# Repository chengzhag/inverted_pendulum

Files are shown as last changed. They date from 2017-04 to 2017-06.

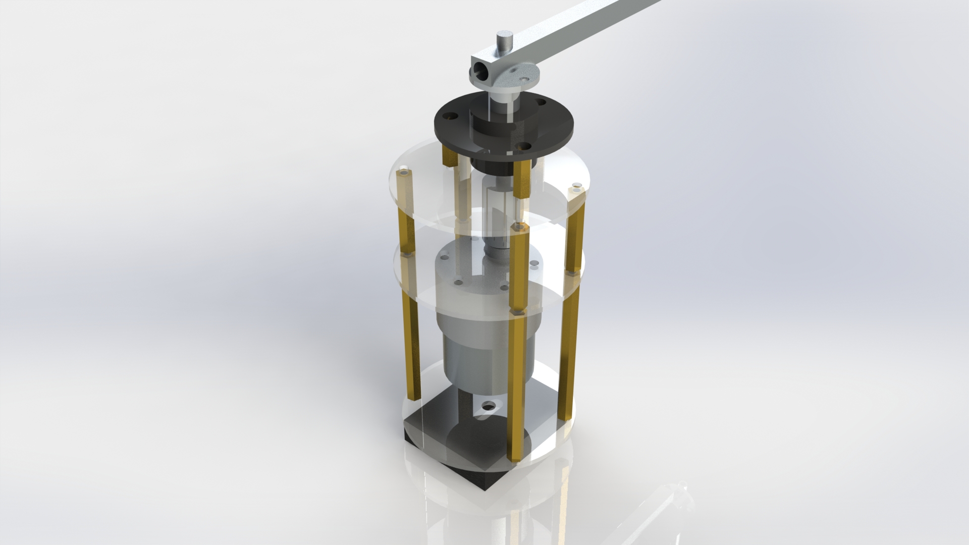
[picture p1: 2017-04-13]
3d/装配体/驱动部分渲染图.JPG

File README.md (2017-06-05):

# inverted_pendulum

电子科技大学2017电子设计竞赛校队控制组第一次训练，KZ-3组

小组成员：章程，韦仕才，徐瑶

采用ebox库，vs2015开发环境。[模板和使用说明](https://github.com/pidan1231239/ebox_stm32f103RCT6_VS#ebox_stm32f103rct6_vs)参考队长[章程](https://github.com/pidan1231239)的ebox_stm32f103RCT6_VS

## 机械部分说明

### 材料选取及用途：
- 3mm厚碳板和铜柱作为快装板和电机支撑
- 碳方管作为横梁
- 碳圆管作为摆杆
- 铝棒作为转轴
- 底部用三脚架支撑
- 连接处用法兰联轴器以及五转六的电机联轴以及绑扎带固定
- 采用导电滑环防止绕线

## 软件部分说明

### 重新编写编码器驱动```encoder_timer```
- 可用引脚：高级定时器和通用定时器可以将ch1和ch2配置成正交编码器AB相输入
- TIM1~TIM4可用io口如下：
  - TIM1:PA8 PA9
  - TIM2:PA0 PA1
  - TIM3:PA6 PA7
  - TIM4:PB6 PB7
- 本次倒立摆设计采用TIM1和TIM3配置正交编码器。用TIM2配置PWM控制电机

### 编写电机驱动```encoder_motor.h```
- 设置速度和位置模式以及PID初始化

### 将光编码器作为绝对编码器使用
- 计算摆杆的角加速度和角速度，以弧度制为单位

### 采用四级PID控制
- 对摆杆角度、摆杆角速度、横梁角度、横梁角速度进行PID算法控制

### 采用状态机和四个独立键盘对倒立摆进行模式切换
- 选择io如下：PB12 PB13 PB14 PB15
- 对应模式：```Swing SwingInvert Invert Round```

### 用freertos设置进程
- 实现多任务并行处理

## 电路部分说明
- 电路组成：
  - LM2596S-5.0作为降压模块
  - tb6612作为电机驱动
  - stm32f103c8t6最小系统作为主控
  - 四个独立按键
- 电路设计：
  - 电机驱动模块插座
  - c8t6最小系统板插座
  - 降压模块插座
  - 4pin xh2.56光编码器接口
  - 6pin xh2.56电机接口
  - 4pin xh2.56延长线
  - 12v电池插头

## 有限状态机
### 设计思路
- 状态以类的方式存储
- 状态的entry、work、exit函数以指针方式存储
- 状态的向外转移列表以类链表存储

### class FiniteStateMachine
> 有限状态机类
- 切换状态
  - 执行上一个State的exit函数
  - （执行状态转移函数，需要状态过渡时使用）
  - 设置当前状态指针
  - 执行下一个State的entry函数
- refresh函数中
  - 调用状态的work函数
  - 判断是否满足下列条件，如果满足，进行转移
    - 满足状态的向外转移列表中事件对应的bool判别式（函数，传入event参数）

### class FiniteStateMachineState
> 状态类
- 包含entry、work、exit函数指针
  - 提供接口对函数指针进行初始化
  - 提供接口对函数指针进行调用
- 向外转移列表（链表）
  - 在FiniteStateMachine调用refresh进行转移判断时对当前State的列表进行遍历，满足条件则进行转移
  - 提供接口addTransItem用以增加表项
  - 在初始化时可直接将该表传入

### class FiniteStateMachineTrans
> 向外转移列表类，单向链表，自身构成链表头
- 通过next指针形成链表
- 在初始化时可通过before衔接已有的链表
- 包含一个bool代数式（函数）condition
- 包含一个目标State*（状态指针）

### 改进方向
- FiniteStateMachineState添加向外转移表项的函数改为可变参数
- 改进FiniteStateMachineTrans类为FiniteStateMachineTransList和FiniteStateMachineTransItem，成为一个封装完善的单向链表，且具有添加操作
- 考虑以unsigned long型保存event，用多选一的方式表示单个event，这样可以通过或操作完成多个event的表示，将event和condition分离，以event作为触发，condition作为条件

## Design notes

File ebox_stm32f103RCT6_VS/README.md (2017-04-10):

# 第41组软件方向说明

## 1 工程模板

> stm32 + ebox的工程模板已发布到[github](https://github.com/pidan1231239/ebox_stm32f103RCT6_VS)上
在压缩包中对应文件：**ebox_stm32f103RCT6_VS.zip**

- 开发环境采用Visual Studio 2015 + visualGDB，编译器采用keil5的arm编译器，配置过程参考文件：**Visual Studio搭建STM32开发环境（自动补全+跳转+DEBUG**
- 了解ebox的功能和已包含驱动，访问[ebox官网](http://www.eboxmaker.com/)和参考上方github链接中[包含驱动](https://github.com/pidan1231239/ebox_stm32f103RCT6_VS/blob/master/README.md#包含驱动)
- 深入了解[stm32 ebox工程从keil到visual studio的迁移过程](https://github.com/pidan1231239/ebox_stm32f103RCT6_VS/blob/master/README.md#如何将工程搬移到visualgdb上)，和[visualGDB官方教程](https://visualgdb.com/tutorials/arm/keil/)

## 2 开发环境

> 以下必备开发软件务必都装在默认位置！尤其是keil 5，因为visualGDB的工程使用了keil的编译器，引用的是绝对地址

### 2.1 Visual Studio 2015 Community

> 在Microsoft官网下载免费版，并更新至update3

### 2.2 keil 5

> 安装keil for arm，即mdk

### 2.3 VisualGDB

> 安装visualgdb 5.16，文件：**visualgdb516rpj(www.greenxf.com).zip**

### 2.4 VassistX

> 安装VisualAssistX 10.9.2108，文件：**[WWW.WuleBa.COM]Vis.ual.Ass.ist.X 10.9.2108 官.方.原.版+破@jie补丁（Visual Studio 超强插件，吾乐吧软件站分享）.rar**

> 以上环境的配置参考文件:**Visual Studio搭建STM32开发环境（自动补全+跳转+DEBUG）.pdf**

### 2.5 Visual Studio Code

编辑MarkDown，浏览代码等

### 2.6 gihub gui客户端

版本控制，代码共享、合作

## 3. 开发硬件

### 3.1 STM32 F103

> 受限于ebox库，目前任得到维护的只有针对STM32 F103的ebox

### 3.2 RL78/G13 开发套件 R5F100LEA 单片机

> 一款瑞萨的单片机开发板，校队可能会发，为前几届比赛个别控制体的指定用MCU

### 3.3 可能需要的基于linux的开发板，如树莓派

> 图像处理等大计算量运算

## 4 必备技能

### 4.1 C++

> - 要求掌握对象、继承、重载、模板、命名空间等常用知识
> - 开发单片机用

### 4.2 MarkDown

> - 学习此文档中使用的一些基本语法
> - 用于代码文档的编写

### 4.3 github gui客户端

> - 注册github账号，完成官方基础教程
> - 下载安装GitKraken和SourceTree

### 4.4 matlab

> - 用于算法的实验、学习控制理论
> - 其他未知用途

### 4.5 印象笔记

> - 下载手机、电脑客户端
> - 注册账号
> - 记录重要事件
> - 记录分享赛题资料、思考，协同编辑

### 4.6 Processon

> - 一款在线作图应用
> - 注册账号
> - 实时协作
> - 常用系统框图和流程图、思维导图等

### 4.7 SolidWorks 2017

> - 三维制图，零件、装配体
> - 工程图生成：装配图、零件图、剖面、三视图

## 5 统一编程命名规范

- 类名采用首字母大写的驼峰命名法：```class EncoderMotor```
- 函数、变量采用首字母小写的驼峰命名法：```int motorPosition```
- 宏定义，全大写，单词之间用"_"隔开：```#define ENCODER_MOTOR```
- 枚举变量，enum用首字母大写的单词，以"_"隔开：
```cpp
typedef enum
{
  EXTI_Trigger_Rising = 0x08,
  EXTI_Trigger_Falling = 0x0C,  
  EXTI_Trigger_Rising_Falling = 0x10
}EXTITrigger_TypeDef;
```

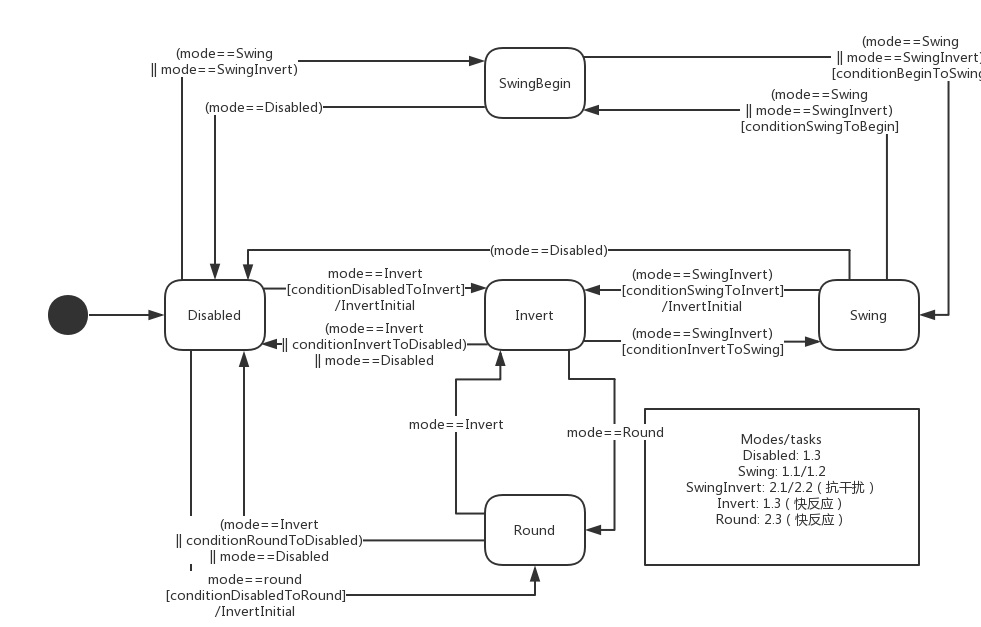
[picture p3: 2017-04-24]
文档/倒立摆状态机.jpg

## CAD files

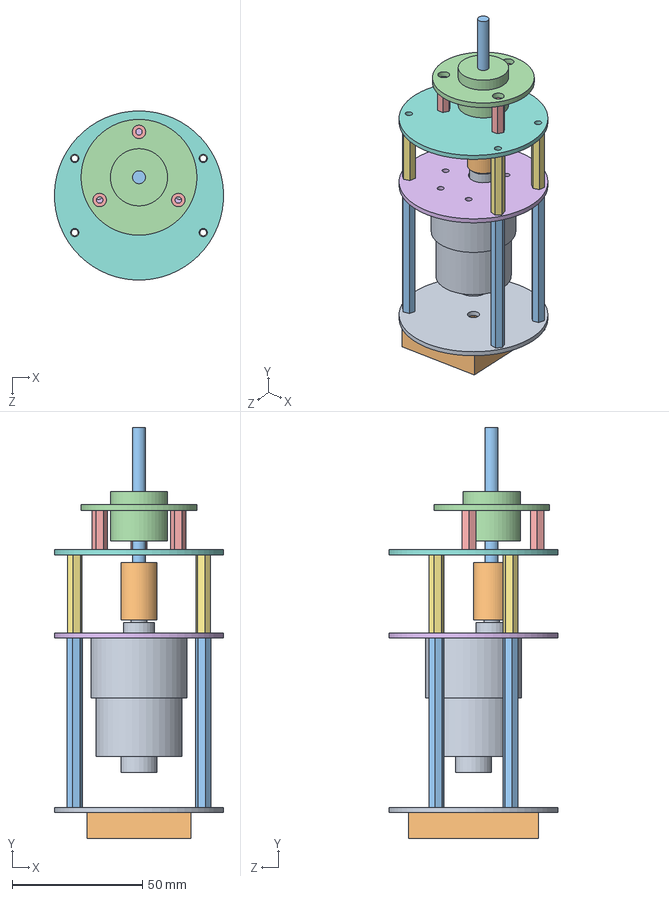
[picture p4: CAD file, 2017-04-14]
3d/装配体/驱动部分.SLDASM
65.0 x 157.9 x 65.0 mm
电机
联轴器5转6
轴_5mm
滑环_5mm
铜柱M3_双通_15mm x 3
电机安装板
铜柱M3_双通_30mm x 4
滑环安装板
快装板电机安装板
快装板
铜柱M3_双通_65mm x 4

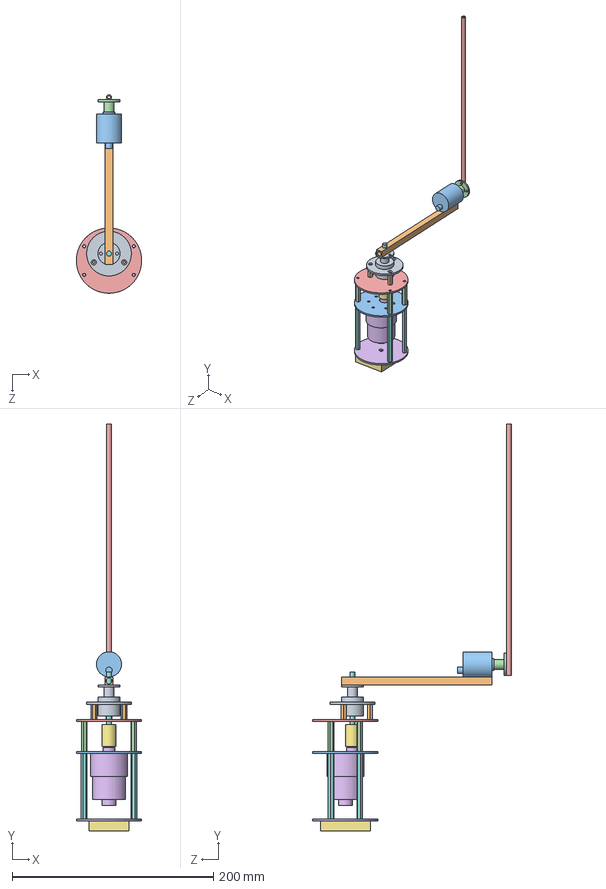
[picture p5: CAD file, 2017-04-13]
3d/装配体/倒立摆.SLDASM
65.0 x 404.8 x 197.5 mm
法兰_5mm
横梁
光编码器
法兰_4mm
摆杆
电机
联轴器5转6
轴_5mm
滑环_5mm
铜柱M3_双通_15mm x 3
电机安装板
铜柱M3_双通_30mm x 4
滑环安装板
快装板电机安装板
快装板
铜柱M3_双通_65mm x 4

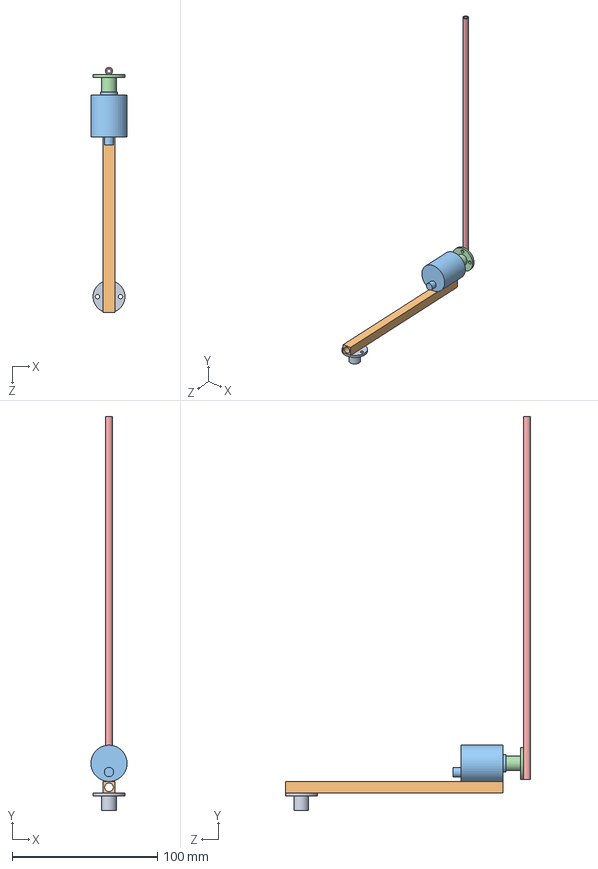
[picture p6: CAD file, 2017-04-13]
3d/装配体/摆杆部分.SLDASM
25.0 x 271.5 x 169.0 mm
法兰_5mm
横梁
光编码器
法兰_4mm
摆杆

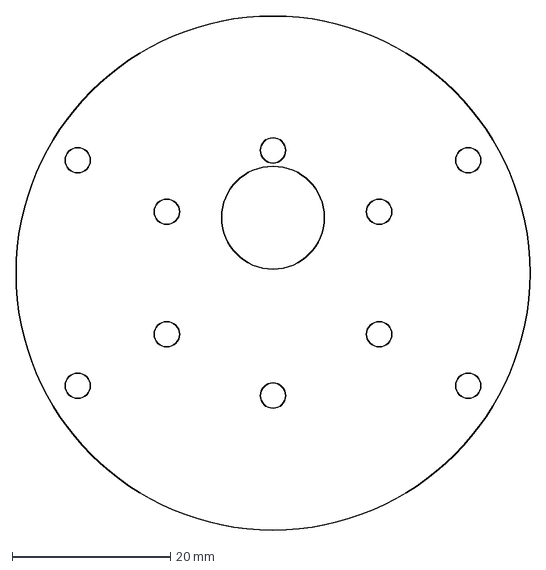
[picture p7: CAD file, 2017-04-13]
3d/雕刻机/电机安装板.DXF
65.0 x 65.0 mm

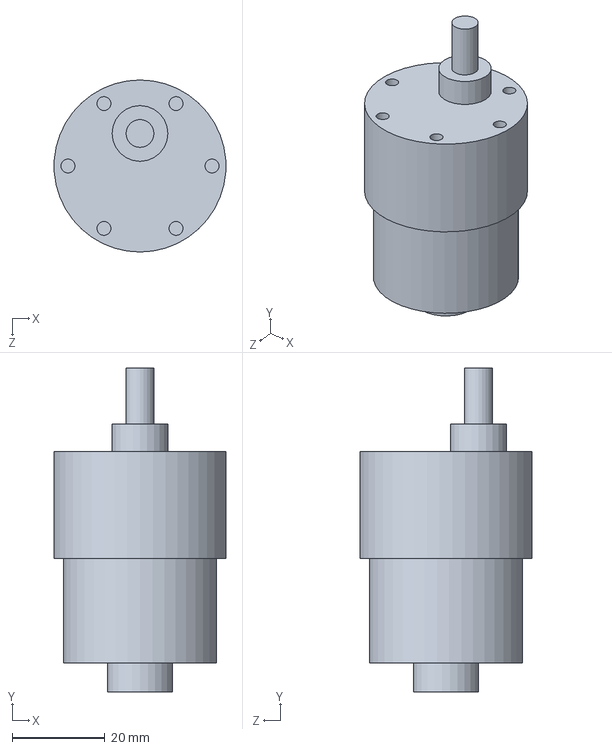
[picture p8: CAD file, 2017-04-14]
3d/零件/电机.SLDPRT
36.9 x 69.7 x 37.0 mm

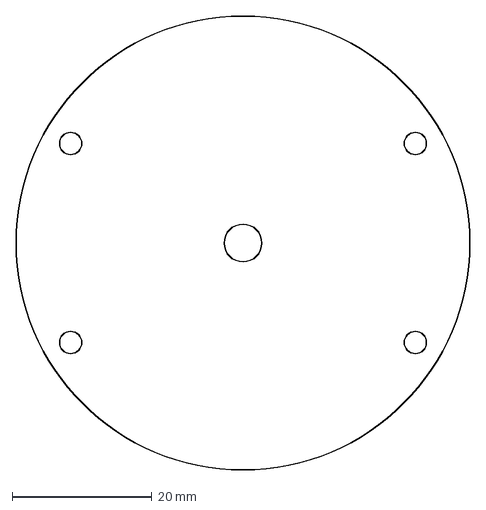
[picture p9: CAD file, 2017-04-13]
3d/雕刻机/快装板电机安装板.DXF
65.0 x 65.0 mm

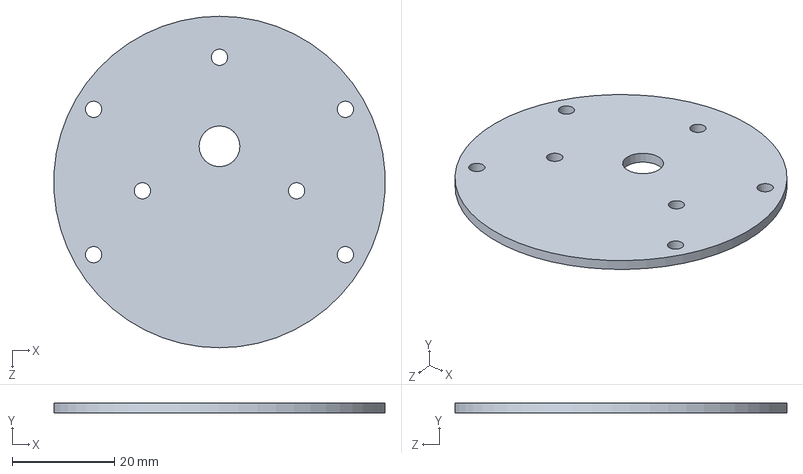
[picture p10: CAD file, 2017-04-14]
3d/零件/滑环安装板.SLDPRT
64.9 x 2.00 x 65.0 mm

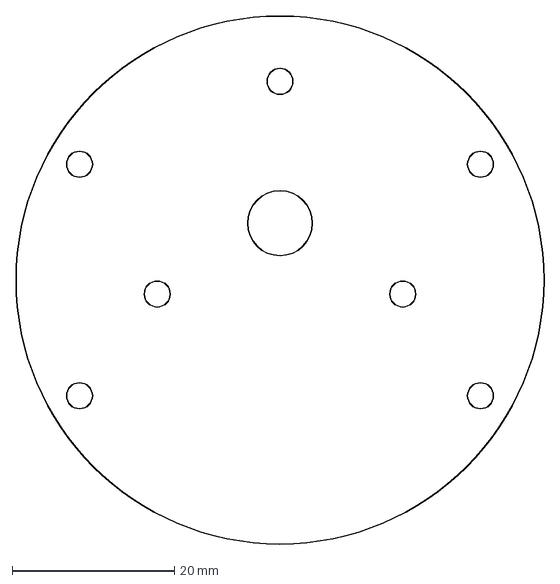
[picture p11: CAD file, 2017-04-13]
3d/雕刻机/滑环安装板.DXF
65.0 x 65.0 mm

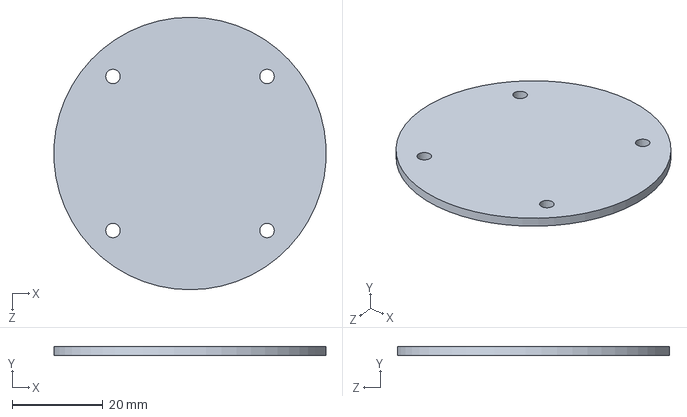
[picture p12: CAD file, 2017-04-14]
3d/零件/快装板电机安装板.SLDPRT
59.9 x 2.00 x 60.0 mm

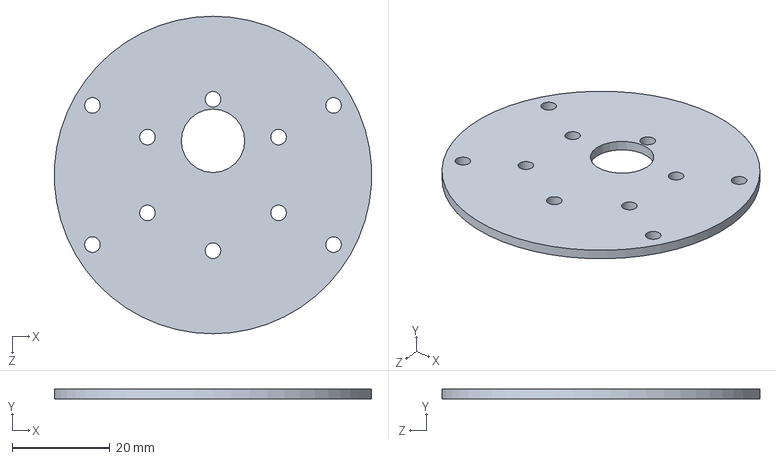
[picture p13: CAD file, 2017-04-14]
3d/零件/电机安装板.sldprt
64.9 x 2.00 x 65.0 mm

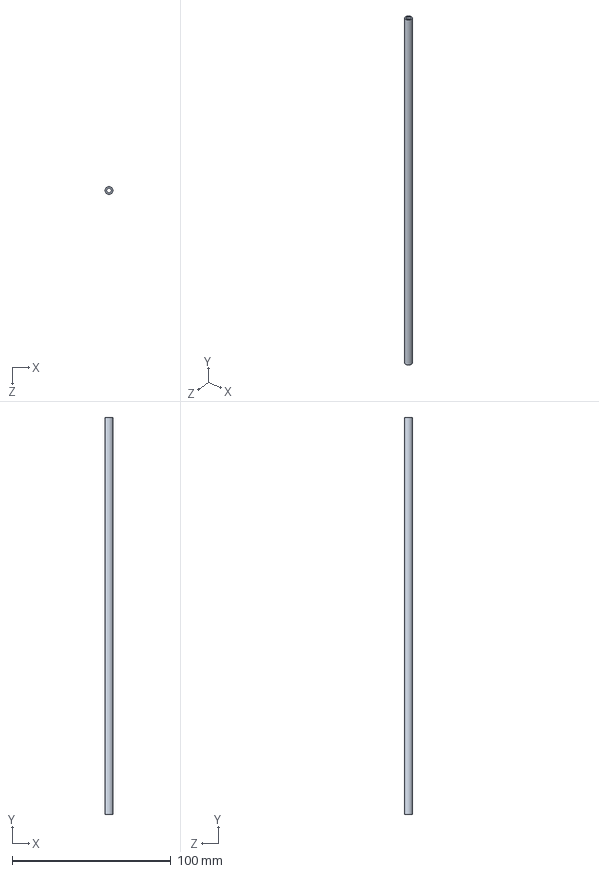
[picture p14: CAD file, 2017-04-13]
3d/零件/摆杆.SLDPRT
5.00 x 250.0 x 5.00 mm

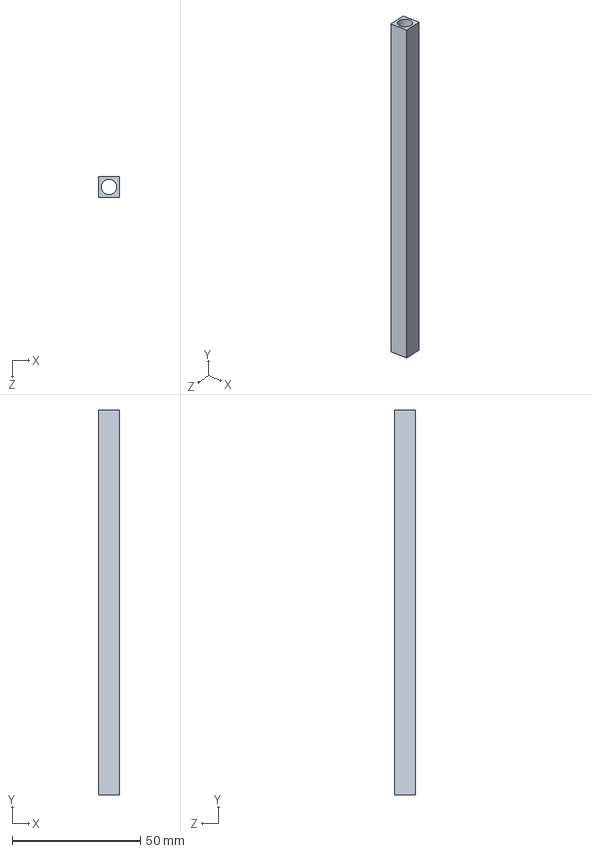
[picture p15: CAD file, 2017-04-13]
3d/零件/横梁.SLDPRT
8.00 x 150.0 x 8.00 mm

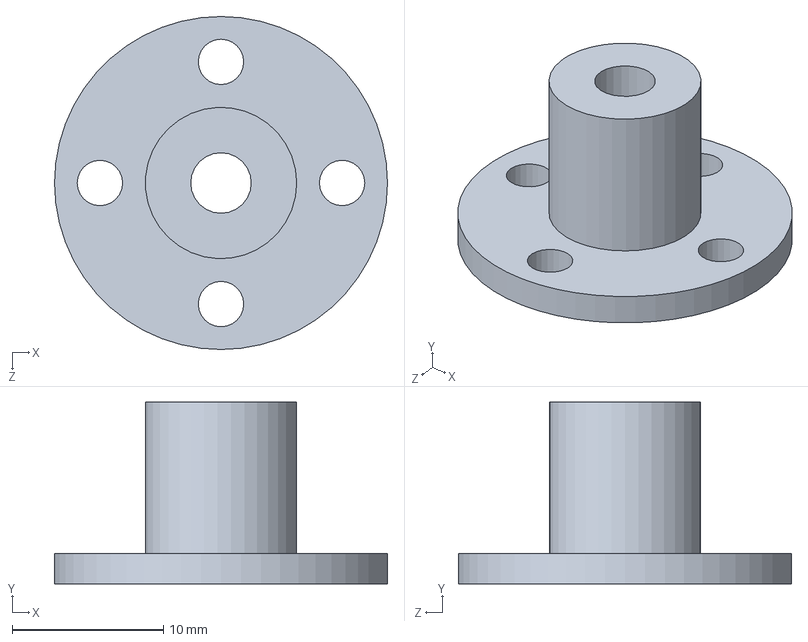
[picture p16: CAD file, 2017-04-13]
3d/零件/法兰_4mm.SLDPRT
22.0 x 12.0 x 22.0 mm

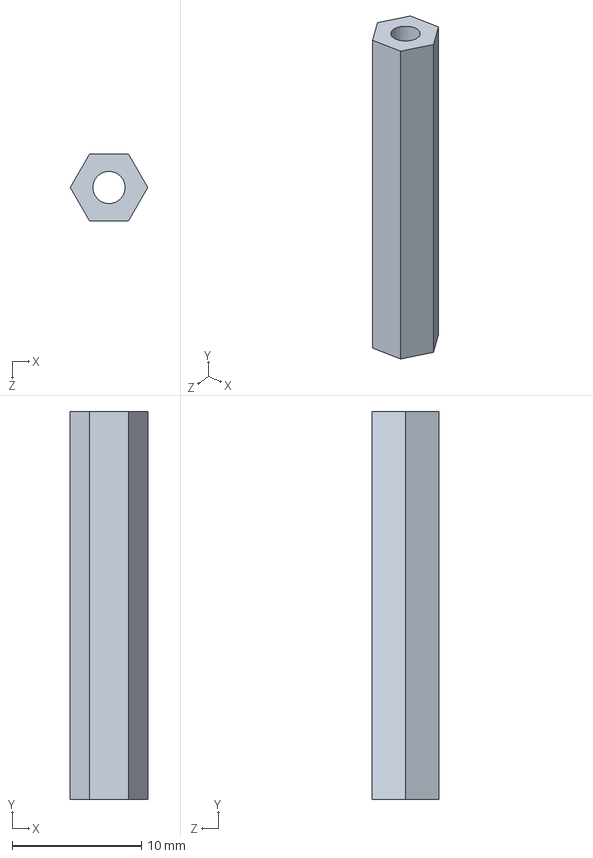
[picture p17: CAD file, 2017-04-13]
3d/零件/铜柱M3_双通_30mm.SLDPRT
6.00 x 30.0 x 5.20 mm

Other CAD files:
3d/图纸/倒立摆.DWG
3d/零件/铜柱M3_双通_65mm.SLDPRT
3d/零件/联轴器5转6.SLDPRT
3d/零件/轴_5mm.SLDPRT
3d/装配体/倒立摆.SLDDRW
3d/零件/光编码器.SLDPRT
3d/零件/快装板.SLDPRT
3d/零件/法兰_5mm.SLDPRT
3d/零件/滑环_5mm.SLDPRT
3d/零件/铜柱M3_双通_15mm.SLDPRT

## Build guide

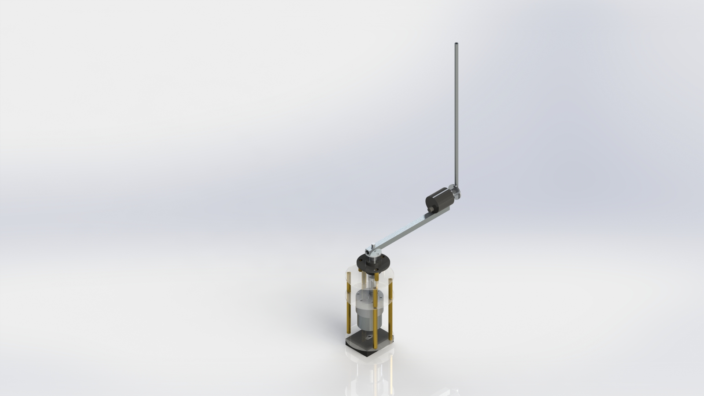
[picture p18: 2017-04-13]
3d/装配体/装配体渲染图.JPG

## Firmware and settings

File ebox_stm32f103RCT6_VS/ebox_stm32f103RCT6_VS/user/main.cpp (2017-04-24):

/**
  ******************************************************************************
  * @file   : *.cpp
  * @author : shentq
  * @version: V1.2
  * @date   : 2016/08/14

  * @brief   ebox application example .
  *
  * Copyright 2016 shentq. All Rights Reserved.         
  ******************************************************************************
 */

#include "ebox.h"
#include "freertos.h"
#include "task.h"
#include "queue.h"
#include "led.h"
#include "Button.h"
#include "inverted_pendulum.h"


#define PID_REFRESH_INTERVAL 0.01

Led led1(&PC13, 1);

InvertedPendulum invertedPendulum(TIM4, TIM3,
	&PA2, &PA1, &PA0,
	2000, 1560, PID_REFRESH_INTERVAL);

Button btnSwing(&PB12, 1);
Button btnSwingInvert(&PB13, 1);
Button btnInvert(&PB14, 1);
Button btnRound(&PB15, 1);

//用于观察波形的全局变量
//float motorRadian = 0;
//float pendulumRadian = 0;

static void vButtonTask(void *pvParameters)
{
	while (1)
	{
		vTaskDelay(20 / portTICK_RATE_MS);
		uart1.printf("%f\t%f\t%f\t%f\t%f\r\n",
			invertedPendulum.getBeamRadian(),
			invertedPendulum.getBeamPalstance(),
			invertedPendulum.getPendulumRadian(),
			invertedPendulum.getPendulumPalstance(),
			invertedPendulum.getPendulumAcceleration()
		);

		//用于观察波形的全局变量
		//motorRadian = invertedPendulum.getBeamRadian();
		//pendulumRadian= invertedPendulum.getPendulumRadian();

		btnSwing.loop();
		btnSwingInvert.loop();
		btnInvert.loop();
		btnRound.loop();

		if (btnSwing.click())
		{
			if (invertedPendulum.getMode() != Inverted_Pendulum_Mode_Swing)
			{
				invertedPendulum.setMode(Inverted_Pendulum_Mode_Swing);
			}
			else
			{
				invertedPendulum.setMode(Inverted_Pendulum_Mode_Disabled);
			}
			led1.toggle();
		}
		if (btnSwingInvert.click())
		{
			if (invertedPendulum.getMode() != Inverted_Pendulum_Mode_SwingInvert)
			{
				invertedPendulum.setMode(Inverted_Pendulum_Mode_SwingInvert);
			}
			else
			{
				invertedPendulum.setMode(Inverted_Pendulum_Mode_Disabled);
			}
			led1.toggle();
		}
		if (btnInvert.click())
		{
			if (invertedPendulum.getMode() != Inverted_Pendulum_Mode_Invert)
			{
				invertedPendulum.setMode(Inverted_Pendulum_Mode_Invert);
			}
			else
			{
				invertedPendulum.setMode(Inverted_Pendulum_Mode_Disabled);
			}
			led1.toggle();
		}
		if (btnRound.click())
		{
			if (invertedPendulum.getMode() != Inverted_Pendulum_Mode_Round)
			{
				invertedPendulum.setMode(Inverted_Pendulum_Mode_Round);
			}
			else
			{
				invertedPendulum.setMode(Inverted_Pendulum_Mode_Disabled);
			}
			led1.toggle();
		}
	}
}


static void vPIDTask(void *pvParameters)
{
	while (1)
	{
		vTaskDelay(PID_REFRESH_INTERVAL*1000 / portTICK_RATE_MS);
		invertedPendulum.refresh();
	}
}


void setup()
{
    ebox_init();
    uart1.begin(115200);
	led1.begin();
	btnSwing.begin();
	btnSwingInvert.begin();
	btnInvert.begin();
	btnRound.begin();

	invertedPendulum.begin();
	invertedPendulum.setMode(Inverted_Pendulum_Mode_Disabled);


	//设置RTOS进程
	set_systick_user_event_per_sec(configTICK_RATE_HZ);
	attach_systick_user_event(xPortSysTickHandler);

	xTaskCreate(vButtonTask, "Debug", configMINIMAL_STACK_SIZE, (void *)0, NULL, NULL);
	xTaskCreate(vPIDTask, "PID", configMINIMAL_STACK_SIZE, (void *)0, NULL, NULL);
	vTaskStartScheduler();
}

int main(void)
{
    setup();

    while(1)
    {
    }
}

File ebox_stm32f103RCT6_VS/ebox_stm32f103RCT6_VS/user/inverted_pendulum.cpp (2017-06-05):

#include "inverted_pendulum.h"

EncoderPendulum::EncoderPendulum(TIM_TypeDef *TIMx, unsigned int numPerRound /*= 2000*/) :
	EncoderTimer(TIMx),
	npr(numPerRound)
{

}

void EncoderPendulum::refresh()
{
	oldDiff = getDiff();
	EncoderTimer::refresh();
	ddiff = getDiff() - oldDiff;
}

float EncoderPendulum::getRadian()
{
	long posTemp = getPos();
	if (posTemp >= 0)
	{
		return getPos() % npr / (float)npr * 2 * PI - PI;
	}
	else
	{
		return (npr - (-getPos()) % npr) / (float)npr * 2 * PI - PI;
	}
}

float EncoderPendulum::getRadianDiff()
{
	return getDiff() / (float)npr * 2 * PI;
}

float EncoderPendulum::getRadianDDiff()
{
	return ddiff / (float)npr * 2 * PI;
}

MotorBeam::MotorBeam(TIM_TypeDef *TIMx, Gpio *motorPinA, Gpio *motorPinB,
	Gpio *motorPinPwm, unsigned int numPerRound /*= 1560*/,
	Encoder_Motor_Target_Typedef controlTarget /*= Encoder_Motor_Target_Position*/, float refreshInterval /*= 0.005*/) :
	EncoderMotor(TIMx, motorPinA, motorPinB, motorPinPwm,
		controlTarget, refreshInterval),
	npr(numPerRound)
{

}

float MotorBeam::getRadian()
{
	return getPos() / (double)npr * 2 * PI;
}

float MotorBeam::getRadianDiff()
{
	return getPosDiff() / (float)npr * 2 * PI;
}




void InvertedPendulum::workDisabled()
{
	motor.setPercent(0);
	pendulumRadian = getPendulumRadian();
}

bool InvertedPendulum::conditionDisabledToSwingBegin(int event)
{
	return (event == Inverted_Pendulum_Mode_Swing || event == Inverted_Pendulum_Mode_SwingInvert);
}

bool InvertedPendulum::conditionDisabledToInvert(int event)
{
	return (event == Inverted_Pendulum_Mode_Invert
		&& (pendulumRadian < enRadThres && pendulumRadian>-enRadThres));
}

bool InvertedPendulum::conditionDisabledToRound(int event)
{
	return (event == Inverted_Pendulum_Mode_Round
		&& (pendulumRadian < enRadThres && pendulumRadian>-enRadThres));
}

void InvertedPendulum::workSwingBegin()
{
	motor.setPercent(50);
	pendulumRadian = getPendulumRadian();
}

bool InvertedPendulum::conditionSwingBeginToSwing(int event)
{
	return ((event == Inverted_Pendulum_Mode_Swing || event == Inverted_Pendulum_Mode_SwingInvert)
		&& (pendulumRadian < PI / 1.5 && pendulumRadian>-PI / 1.5));
}

bool InvertedPendulum::conditionSwingBeginToDisabled(int event)
{
	return (event == Inverted_Pendulum_Mode_Disabled);
}

void InvertedPendulum::entryInvert()
{
	resetPID();
	setTargetBeamRadian(getBeamRadian());
	setTargetBeamPalstance(0);
}

void InvertedPendulum::workInvert()
{
	refreshPID();
	pendulumRadian = getPendulumRadian();
}

bool InvertedPendulum::conditionInvertToDisabled(int event)
{
	return ((event == Inverted_Pendulum_Mode_Invert
		&& (pendulumRadian >= enRadThres || pendulumRadian <= -enRadThres))
		|| event == Inverted_Pendulum_Mode_Disabled);
}

bool InvertedPendulum::conditionInvertToRound(int event)
{
	return (event == Inverted_Pendulum_Mode_Round);
}

bool InvertedPendulum::conditionInvertToSwing(int event)
{
	return (event == Inverted_Pendulum_Mode_SwingInvert
		&& (pendulumRadian >= enRadThres || pendulumRadian <= -enRadThres));
}

void InvertedPendulum::entryRound()
{
	resetPID();
	setTargetBeamRadian(getBeamRadian());
	setTargetBeamPalstance(2);
}

void InvertedPendulum::workRound()
{
	pendulumRadian = getPendulumRadian();

	//设置横梁目标速度
	//对横梁实际角度与目标角度进行判断
	if (abs(getBeamRadian() - getTargetBeamRadian()) < PI)
	{
		setTargetBeamRadian(getTargetBeamRadian() + targetBeamPalstance*refreshInt);
	}
	else
	{
		if (getBeamRadian() - getTargetBeamRadian() > 0)
		{
			setTargetBeamRadian(getBeamRadian() - PI);
		}
		else
		{
			setTargetBeamRadian(getBeamRadian() + PI);
		}
	}

	refreshPID();
}

bool InvertedPendulum::conditionRoundToInvert(int event)
{
	return (event == Inverted_Pendulum_Mode_Invert);
}

bool InvertedPendulum::conditionRoundToDisabled(int event)
{
	return ((event == Inverted_Pendulum_Mode_Round
		&& (pendulumRadian >= enRadThres || pendulumRadian <= -enRadThres))
		|| event == Inverted_Pendulum_Mode_Disabled);
}

void InvertedPendulum::workSwing()
{
	refreshSwing();
	pendulumRadian = getPendulumRadian();
}

////衔接链表末尾的state初始化方式，必须注意初始化顺序是按声明顺序！！！
//InvertedPendulum::InvertedPendulum(TIM_TypeDef *TIMpendulum,
//	TIM_TypeDef *TIMmotor, Gpio *motorPinA, Gpio *motorPinB, Gpio *motorPinPwm,
//	unsigned int nprPendulum /*= 2000*/, unsigned int nprMotor /*= 1560*/, float refreshInterval /*= 0.005*/) :
//	encoder(TIMpendulum, nprPendulum),
//	motor(TIMmotor, motorPinA, motorPinB, motorPinPwm,
//		nprMotor, Encoder_Motor_PID_Disabled, refreshInterval),
//	refreshInt(refreshInterval),
//	enRadThres(PI / 3),
//	mode(Inverted_Pendulum_Mode_Disabled),
//	targetBeamPalstance(0),
//	targetBeamRadian(0),
//	//初始化有限向量机
//	fsm(&stateDisabled),
//	//初始化stateDisabled的转出列表
//	transDisabledToSwingBegin(this, &InvertedPendulum::conditionDisabledToSwingBegin, &stateSwingBegin),
//	transDisabledToInvert(this, &InvertedPendulum::conditionDisabledToInvert, &stateInvert, &transDisabledToSwingBegin),
//	transDisabledToRound(this, &InvertedPendulum::conditionDisabledToRound, &stateRound, &transDisabledToInvert),
//	stateDisabled(this, &InvertedPendulum::workDisabled, NULL, NULL, &transDisabledToSwingBegin),
//	//初始化stateSwingBegin的转出列表
//	transSwingBeginToSwing(this, &InvertedPendulum::conditionSwingBeginToSwing, &stateSwing),
//	transSwingBeginToDisabled(this, &InvertedPendulum::conditionSwingToDisabled, &stateDisabled, &transSwingBeginToSwing),
//	stateSwingBegin(this, &InvertedPendulum::workSwingBegin, NULL, NULL, &transSwingBeginToSwing),
//	//初始化stateInvert的转出列表
//	transInvertToDisabled(this, &InvertedPendulum::conditionInvertToDisabled, &stateDisabled),
//	transInvertToRound(this, &InvertedPendulum::conditionInvertToRound, &stateRound, &transInvertToDisabled),
//	transInvertToSwing(this, &InvertedPendulum::conditionInvertToSwing, &stateSwing, &transInvertToRound),
//	stateInvert(this, &InvertedPendulum::workInvert, &InvertedPendulum::entryInvert, NULL, &transInvertToDisabled),
//	//初始化stateRound的转出列表
//	transRoundToInvert(this, &InvertedPendulum::conditionRoundToInvert, &stateInvert),
//	transRoundToDisabled(this, &InvertedPendulum::conditionRoundToDisabled, &stateDisabled, &transRoundToInvert),
//	stateRound(this, &InvertedPendulum::workRound, &InvertedPendulum::entryRound, NULL, &transRoundToInvert),
//	//初始化stateSwing的转出列表
//	transSwingToDisabled(this, &InvertedPendulum::conditionSwingToDisabled, &stateDisabled),
//	transSwingToSwingBegin(this, &InvertedPendulum::conditionSwingToSwingBegin, &stateSwingBegin, &transSwingToDisabled),
//	transSwingToInvert(this, &InvertedPendulum::conditionSwingToInvert, &stateInvert, &transSwingToSwingBegin),
//	stateSwing(this, &InvertedPendulum::workSwing, NULL, NULL, &transSwingToDisabled)
//{
//
//}
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

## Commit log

2017-04-10 初始化工程
2017-04-10 尝试用中断实现旋转编码器，失败
2017-04-10 中断实现正交编码器，单路升降沿触发
2017-04-10 实现两路升降触发，精度加倍，封装成驱动文件
2017-04-10 测试了freeRTOS在被编码器中断打断下的运行情况
2017-04-10 完成TB6612FNG驱动
2017-04-10 更新小组软件方向说明
2017-04-11 完成编码器电机pid位置控制，未整定pid，注意pid类要先设置间隔时间，再设置pid值！！
2017-04-12 添加position全局变量，供pid整定
2017-04-12 添加3d文件夹，完成滑环建模
    [滑环5mm.SLDPRT]
2017-04-12 完成单双通铜柱以及电机的建模
    [3cm单通铜柱.SLDPRT, 3cm铜柱.SLDPRT, 电机.SLDPRT]
2017-04-12 完成零件的建模
    [光编码器.SLDPRT, 单通铜柱3cm.SLDPRT, 快装板.SLDPRT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]
2017-04-12 电机装配体建模中
    [单通铜柱3cm.SLDPRT, 滑环安装板.SLDPRT, 电机安装板.sldprt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]
2017-04-12 把long long改为long，两者无区别
2017-04-13 重新建立电机装配体，消除错误，需要完善电机建模
    [光编码器.SLDPRT, 快装板.SLDPRT, 法兰5mm.SLDPRT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]
2017-04-13 改名电机驱动、编码器驱动的成员为缩写
2017-04-13 更新倒立摆readme
2017-04-13 完成驱动部分装配体
    [快装板电机安装板.DXF, 快装板电机安装板.SLDPRT, 滑环_5mm.SLDPRT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]
2017-04-13 更新电机编码器磁铁
    [电机.SLDPRT, 驱动部分.SLDASM]
2017-04-13 增加工程图
    [倒立摆.DWG, 倒立摆.SLDASM, 倒立摆.SLDDRW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]
2017-04-13 更新渲染图
2017-04-13 更改startup为md，用于C8T6
    [倒立摆.SLDASM]
2017-04-13 注意还要将编译器的define选项改成MD
2017-04-14 更新led闪烁
2017-04-14 纠错电机建模，配置编码器上拉输入
    [快装板电机安装板.SLDPRT, 滑环安装板.SLDPRT, 电机.SLDPRT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]
2017-04-15 更新定时器编码器驱动，尚待更新long型位置保存
2017-04-15 更新官方库编码器驱动，修复bug，完成电机角度控制pid
2017-04-15 修改变量名，开始设计摆杆角度PID控制
2017-04-15 添加横梁位置控制
2017-04-15 更新注释
2017-04-16 更新电机速度控制驱动
2017-04-16 更新电机速度控制PID
2017-04-18 完善摆杆角度和衡量位置的PID控制
2017-04-18 修复电机驱动refresh函数的模式判断bug
2017-04-18 完成100hz刷新率下的PID调试。改进摆杆倒下判断条件
2017-04-18 更改刷新率为200HZ
2017-04-19 目标角度设为1000
2017-04-21 封装倒立摆类，去除ebox不必要的实例化io等，TODO: 调电机pos模式PID，消除控制过程中的非线性，调倒立摆PID
2017-04-21 添加倒立使能，TODO: 改PID控制量，考虑更改刷新率。调PID，增强抗干扰性能
2017-04-22 新建倒立摆头文件，去除tan、atan操作
2017-04-22 完善倒立摆类，添加获取横梁、摆杆角速度方法，TODO: 重新构造PID控制环路
2017-04-22 根据论文重构PID控制环路。TODO: 添加起摆控制
2017-04-22 添加摆杆角加速度获取函数
2017-04-22 为倒立摆类增加获取角度、角速度、角加速度函数，统一标准单位
2017-04-22 为倒立摆类添加模式设置、起摆模式
2017-04-22 完成四个PID的整定。TODO: 添加开始控制重置PID数值功能
2017-04-22 完成倒下时的PID重置、添加设置横梁目标角度函数。TODO: 在设置横梁目标角度时，还要对横梁角速度PID进行设置
2017-04-22 添加横梁速度控制。TODO: 更改速度控制方法，不以当前位置为起点增加目标角度
2017-04-22 修改控制量为电机输出百分比，为电机增加失能PID模式，
2017-04-22 更新速度控制
2017-04-23 用ifelse实现的倒立摆有限状态机。TODO: 用对象实现有限状态机
2017-04-23 完成基于函数指针的有限状态机类
2017-04-23 完成基于类的成员函数指针的有限状态机，去除有限状态机库（考虑以后封装）。修正uml状态图。
2017-04-23 完成按钮切换模式
2017-04-24 修复状态机bug，更新conditionSwingToInvert
2017-04-24 微调横梁速度PID
2017-04-24 更新状态图，解决被覆盖的问题
2017-04-24 更改一些重复设置的语句
2017-04-25 上传答辩ppt，更新README
2017-04-27 添加文档文件夹
2017-06-05 添加fsm类，更新readme排版和fsm说明
